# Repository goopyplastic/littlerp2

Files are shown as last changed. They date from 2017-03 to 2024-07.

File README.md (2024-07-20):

# LittleRP2
LittleRP2 Open Source Resin Printer  

---

## About

The LittleRP2 is the an update to the LittleRP Open Source Resin Printer that adds additional functionality as well as refinements. Some of the primary differences between the LittleRP and the LittleRP2 are:

### Flexibilty:
- Wider foodprint to allow for additional vat options
- Self-sourceable configurable vat
- Extended height option
- Convertable to larger build area
- Additional controller shield options
- Additional supported projectors
- MGN12 rail option
- TR8x2 Leadscrew option
- Rear shutter access added
- Common vat nut-trap holddowns

### Refinement
- Quiet operation (using TMC2100 drivers and Astrosyn dampner)
- Hinged hood
- Bent non-glued hood option
- Solid build plate
- Z-limit switch
- Stepper driven shutter / limit switch option
- Sockethead adjustment for build plate leveling
- Increased rigidity of top panel attachment

### Greater Precision and Print Quality
- 25 Micron X/Y options for Acer X152H and Optoma HD37 projectors.
- Astrosyn dampner decouples leadscrew non-eccentricity.

---

## Build Size:
Dimensions vary depending on selected projector but typically projection sizes for the standard height LittleRP2 are:

X: 60-72mm / 110-120mm (w/ Extended Build Area Addon)
Y: 42-45mm / 70-75mm (w/ Extended Build Area Addon)
Z: 100mm / 200mm (w/ Extended Height Version)

(Build size is now expandable up to 120mm (x) 80mm (y) with the new Extended Build Area Addon).

---

## Recommended Projectors:

### Require Focus Modification
- Acer X152H (25 micron x/y capable) NEW
    * (link removed)
- Optoma HD37 (25 micron x/y capable) NEW
    * (Use +7 or +10 diopter close-up filters)
- Acer P1283
    * (https://www.youtube.com/watch?v=d2-g494IS9s)
- Acer X1240
    * (http://imgur.com/a/FOgXW)
- Acer H5380BD NEW
    * (Modification Identical to P1283)
- Viewsonic PJD5255 NEW
- Hitachi CP-DX250 / CP-DX300 (Same as Acer X1240)

### Don't Require Focus Modification
- Acer P1500 (May have focus issues)
- Acer H6510BD (May have focus issues)
- ViewSonic PJD7820HD (Same as Acer P1500) (May have focus issues)

### Projector Mounting Posistions
- (http://imgur.com/a/wpWsU)

---

## Configurations

### LittleRP2 (Standard Height)
LittleRP2LittleRP2

### LittleRP2 Extended Height
LittleRP2 Extended HeightLittleRP2 Extended Height

### LittleRP2 Extended Build Area (Option)
LittleRP2 Extended Build Area

---

## Discussion Thread
- (http://www.buildyourownsla.com/forum/viewtopic.php?f=19&t=5717)

---

## Build Guides

LittleRP2 Build Guide
- (http://imgur.com/a/cm6a2)

LittleRP2 Tall Variant Build Guide
- (http://imgur.com/a/tlTSK)

LittleRP2 Integrated Vat Build Guide
- (http://imgur.com/a/Z1Eb6)

LittleRP2 Expanded Build Area Option Build Guide
- (http://imgur.com/a/ujMIq)

---

## Source File Organization:

DXF - DXF files for lasercut parts.  
STL - STL files for 3D printed parts.

---

## Bill of Materials

LittleRP 2 BOM Checklist - Fastener Box Sub-Bags
- (https://drive.google.com/open?id=1yqt8eWypYL61TpWnnlkjNs6nJOw5RkLmACgm6qkCx2w)

LittleRP 2 BOM Checklist - Packing
- (https://drive.google.com/open?id=1wPVTCZptSK_STgUEYxKO7_aabrpSXejBZ3x2O9j5VzU)

LittleRP 2 PCB Components
- (https://drive.google.com/open?id=12SPEIWxH564DaQywE27lV3rEJNsK8UbMoX9kLrx8uh4)

---

LittleRP2 Hardware / Software is licensed under the Creative Commons BY-SA 3.0 or greater license: https://creativecommons.org/licenses/by-sa/3.0/

You are free to:  
Share — copy and redistribute the material in any medium or format  
Adapt — remix, transform, and build upon the material  
for any purpose, even commercially.

The licensor cannot revoke these freedoms as long as you follow the license terms.

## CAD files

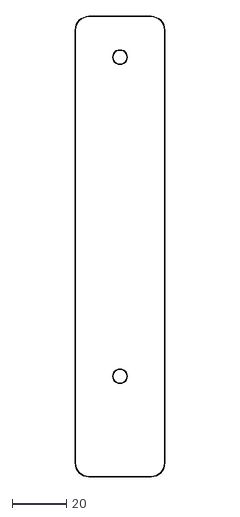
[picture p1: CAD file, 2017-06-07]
DXF/panel_bottom_cutout.DXF
33.0 x 169.6

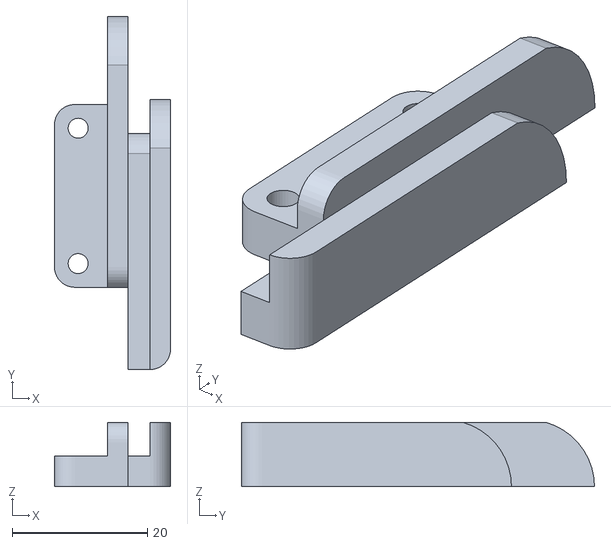
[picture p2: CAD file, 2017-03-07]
STL/hood_extension_lock (tall) (repaired).stl
17.1 x 52.1 x 9.50

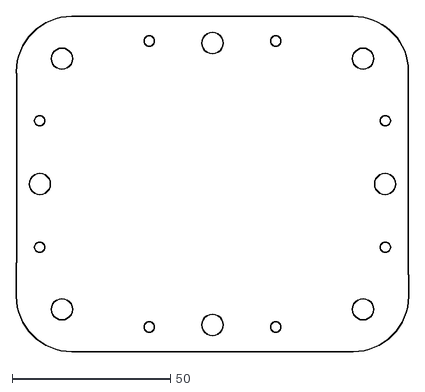
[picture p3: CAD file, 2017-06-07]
DXF/vat_fep.DXF
124.0 x 106.0

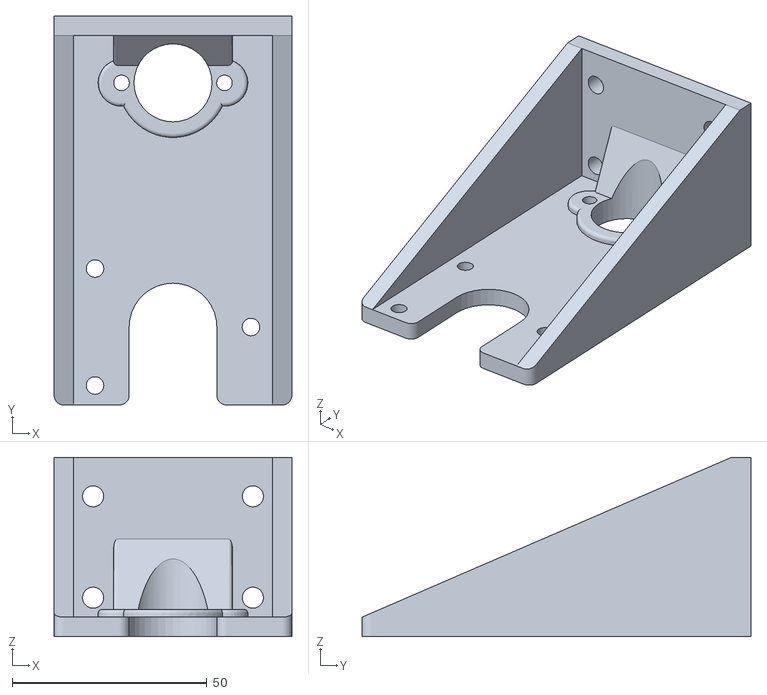
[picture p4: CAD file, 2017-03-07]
STL/zarm_antibacklash (repaired).stl
61.0 x 99.8 x 46.0

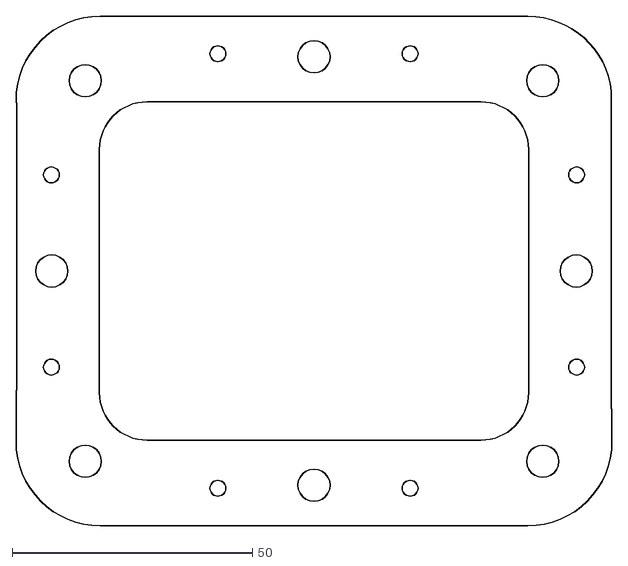
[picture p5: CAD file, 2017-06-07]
DXF/vat_foam.DXF
124.0 x 106.0

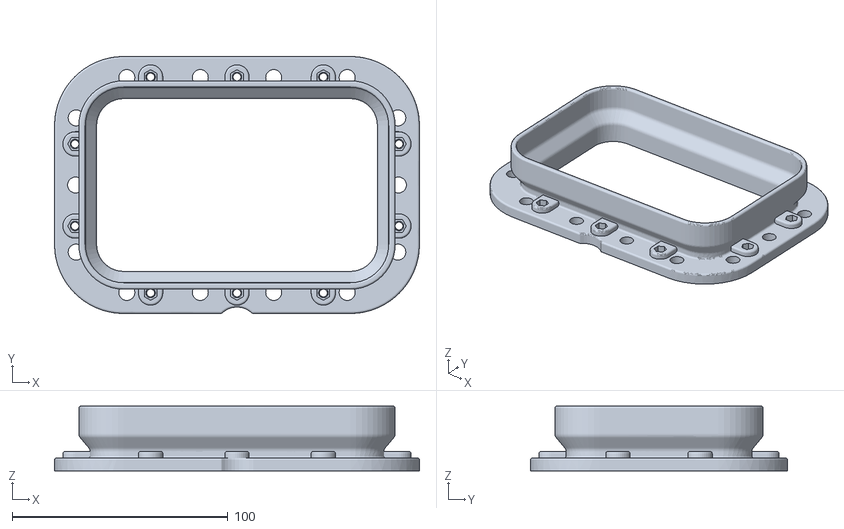
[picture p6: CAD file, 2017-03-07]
STL/vat_top (expanded) (repaired).stl
169.0 x 119.0 x 30.0

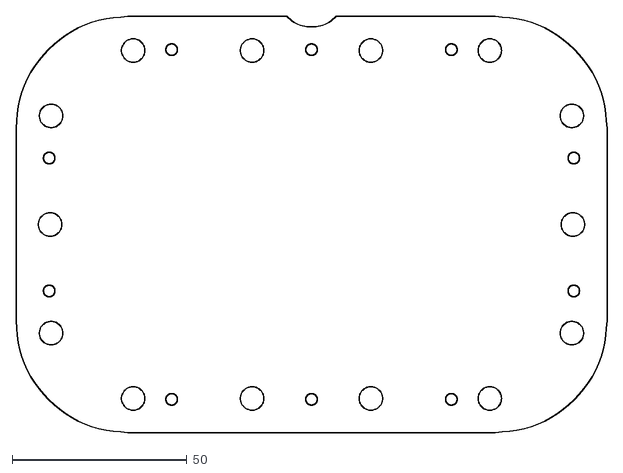
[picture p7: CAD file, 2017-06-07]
DXF/vat_fep (expanded).DXF
169.0 x 119.0

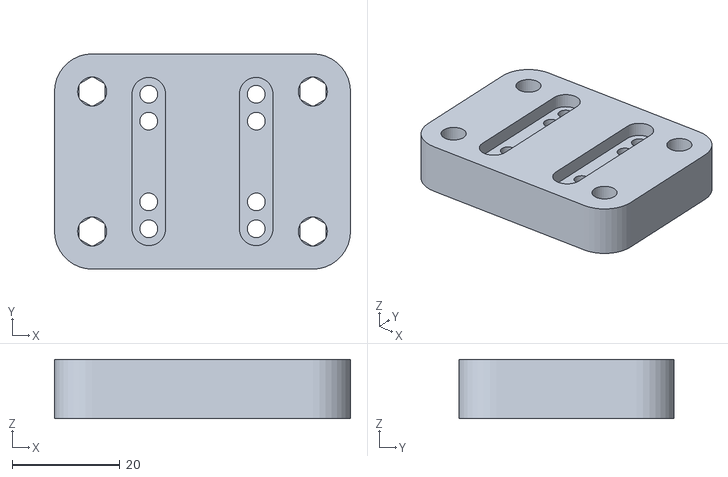
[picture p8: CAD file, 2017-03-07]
STL/option_mgn12adapter (repaired).stl
55.0 x 40.0 x 11.0

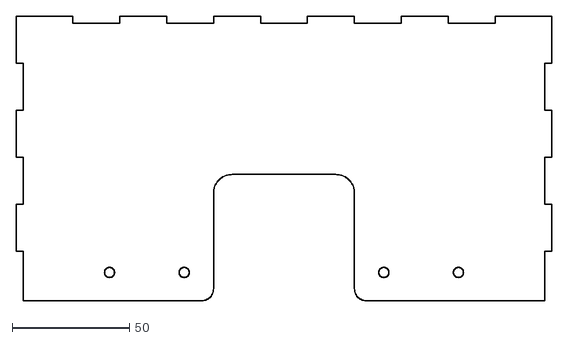
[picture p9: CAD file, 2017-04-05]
DXF/hood_top (glue).DXF
228.0 x 121.0

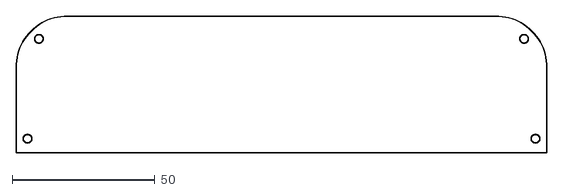
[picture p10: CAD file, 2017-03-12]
DXF/hood_extension_cutout (tall).DXF
186.0 x 48.0

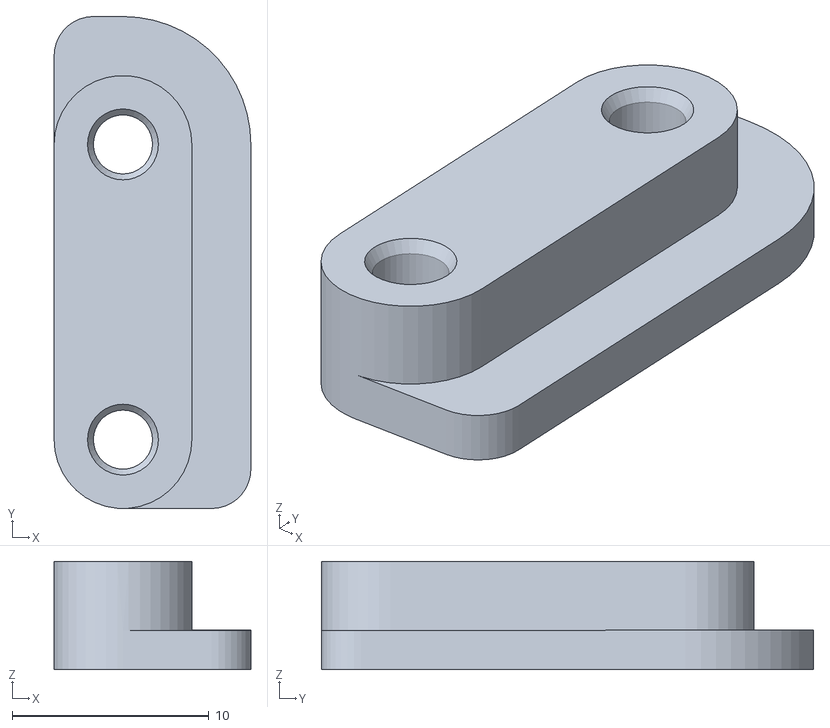
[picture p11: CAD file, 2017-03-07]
STL/hood_extension_side_clamp_mirror (tall) (repaired).stl
10.0 x 25.0 x 5.50

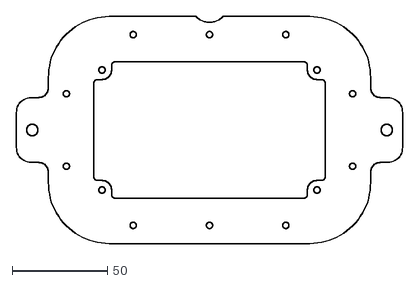
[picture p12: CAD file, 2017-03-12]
DXF/vat_hightension_bottom (expanded).DXF
202.6 x 119.0

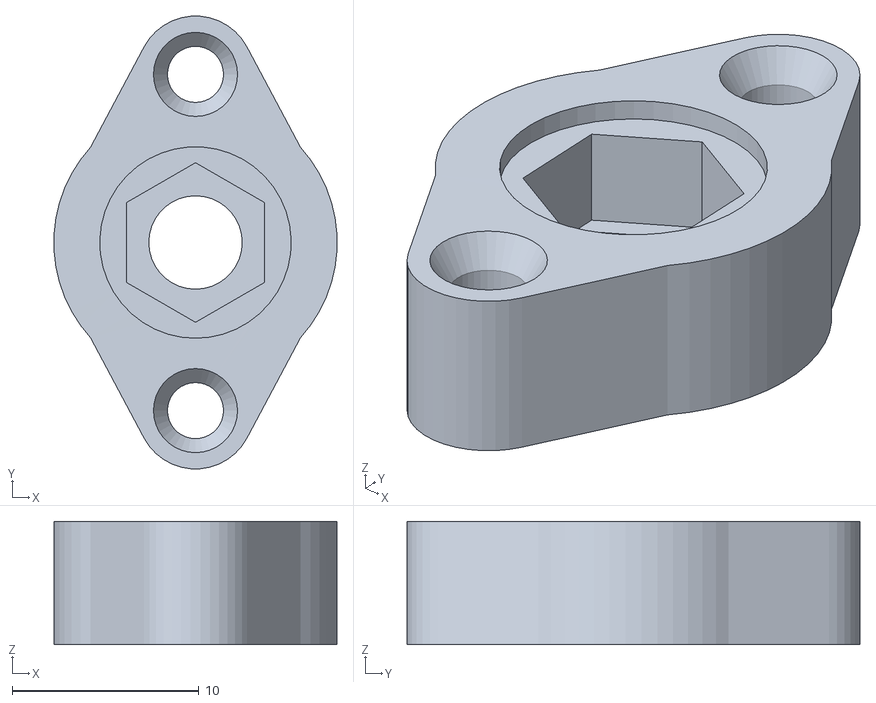
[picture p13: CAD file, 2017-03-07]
STL/vat_m4_nuttrap (repaired).stl
15.2 x 24.2 x 6.60

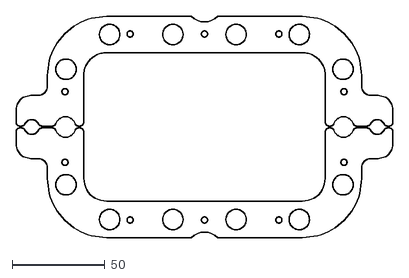
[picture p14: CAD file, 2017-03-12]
DXF/vat_hightension_tensionstop (expanded).DXF
202.6 x 119.0

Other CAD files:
STL/hood_extension_lock_mirror (tall) (repaired).stl
STL/vat_m6_nuttrap (repaired).stl
DXF/vat_foam (expanded).DXF
STL/mirror_holder (repaired).stl
DXF/buildplate_gasket (expanded).DXF
DXF/hood_extension (tall).DXF
DXF/hood_extension_side (tall).DXF
DXF/hood_front (glue).DXF
DXF/hood_side (glue).DXF
DXF/hood_top_brace.DXF
DXF/hood_vanity (expanded).DXF
DXF/mirror_holder_base (expanded).DXF
DXF/mirror_holder_side (expanded).DXF
DXF/panel_bottom.DXF
DXF/panel_discspacer.DXF
DXF/panel_mid (expanded).DXF
DXF/panel_mid.DXF
DXF/panel_projectorbase.DXF
DXF/panel_rear (tall).DXF
DXF/panel_rear.DXF
DXF/panel_side (tall).DXF
DXF/panel_side.DXF
DXF/panel_top.DXF
DXF/projector_hd37foot.DXF
DXF/projector_spacers.DXF
DXF/shutter_manual (expanded).DXF
DXF/shutter_manual.DXF
DXF/vat_hightension_bottom.DXF
DXF/vat_hightension_mid (expanded).DXF
DXF/vat_hightension_mid.DXF
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

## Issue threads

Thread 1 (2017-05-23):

DXF for integrated vat parts?

mhv-shared, 2017-05-23:
Hi, is it possible for you to post the dxf files for the foam insert and FEP film parts shown in the integrated vat build guide?

Also, is there any documentation on the usage of the "hightension" vat parts?

Thanks!

davidfanner, 2017-05-29:
I would be surprised if that happened, seeing as Flexvat is owned by a
different guy..

Regards
David - 083 279 0286

On Tue, May 23, 2017 at 10:11 PM, MakeHaven shared account <
notifications@github.com> wrote:

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

mhv-shared, 2017-05-29:
I think it was probably just an oversight. Anyway, if someone else is looking for them, I've added versions to [my fork](https://github.com/mhv-shared/littlerp2/commit/504366068896fd42e6644972d1c0bf598e1bb739)

goopyplastic, 2017-05-30:
Yes just an oversight, I will get them up. The regular (non expanded) vat is compatible with HTL's films / foams and he has some DXF's online also. I have been meaning to do a high tension video / explanation. I never actually shipped kits with the hightension, it is more just an option if it was needed. You can see the consruction here: http://imgur.com/a/afo7p

The LittleRP2 vat is meant to be run at a fairly low tension, this is to decrease the separation forces (at the cost of film life) we can do this primarily because there is an acrylic window underneath the film. If you wanted to run a window with the central portion open, or needed the film to be at a higher tension for durability reasons then the stock mid plate would start to bow.

The high tension parts basically convert the LittleRP2 vat into a more standard flexvat where the tensioner is part of the vat and the vat is tensioned as a separate unit. Because there is perimeter clamping, you can run higher tension without bowing. You would use different material thicknesses of the tensionstops / windowspacers to achieve different pre-determined tension values (window heights). Using different combinations of 1.5 / 2.5 / 3.0 mm tensionstops / windowspacers you can raise the effect window height in pretty small increments.

These options are also meant as somewhat of a future-proofing, in case the flexvat.com V5 flexvat and seemecnc diy flexvat were no longer offered.

goopyplastic, 2017-06-07:
I have uploaded these files now.

Closed 2017-06-07.

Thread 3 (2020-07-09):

CAD Files

suleymanturkoglu, 2020-07-09:
You can share cad files(step, solidworks...)

goopyplastic, 2020-07-09:
I have added a STEP file of the complete assembly.

Closed 2020-07-09.

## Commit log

2017-07-13 Update README.md
    Added BOM Links
2020-07-09 Add files via upload
    Added STEP File of Assembly
